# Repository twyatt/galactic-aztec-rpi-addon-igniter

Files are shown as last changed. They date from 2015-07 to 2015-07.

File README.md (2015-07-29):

# About
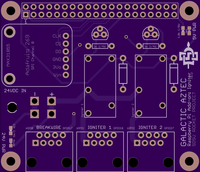
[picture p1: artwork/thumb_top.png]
OSHPark PCB Top Thumbnail

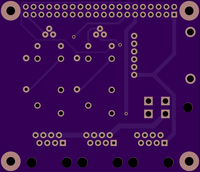
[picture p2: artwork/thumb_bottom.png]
OSHPark PCB Bottom Thumbnail


Custom Raspberry Pi Add-on board used for launching the [Galactic Aztec] rocket to interface with the [Galactic Aztec Igniter Connector]. The board was designed to be stackable with other add-on boards via the designated [pin configuration].

Custom EagleCAD parts on this board can be found in the [SDSU Rocket Eagle Libraries].

## Wiring
The igniter and break wires that ran from the add-on board to the rocket's igniter were [CAT6 cables] that ran thru [RJ45 couplers] and followed the following [T-568B] wiring configurations:

### Igniter
| Pin | Color | Function |
|:---:|:---:|:---:|
| 1 | Orange/White | Supply Voltage |
| 2 | Orange | Ground |
| 3 | Green/White  | Supply Voltage |
| 4 | Blue | Ground |
| 5 | Blue/White | Supply Voltage |
| 6 | Green | Ground |
| 7 | Brown/White  | Supply Voltage |
| 8 | Brown | Ground |

### Break Wire
| Pin | Color | Function |
|:---:|:---:|:---:|
| 1 | Orange/White | 3.3V |
| 2 | Orange | Signal |
| 3 | Green/White  | 3.3V |
| 4 | Blue | Signal |
| 5 | Blue/White | 3.3V |
| 6 | Green | Signal |
| 7 | Brown/White  | 3.3V |
| 8 | Brown | Signal |

# Bill of Materials
| Qty | Description | Part Number | Vendor |
|:---:|---|---:|---|
| 1 | Header Stacking 2x20 Tall 23mm | [1979] | Adafruit |
| 2 | Diode 50V 1A PTH | [1N4001FSCT-ND] | DigiKey  |
| 2 | Transistor NPN 40V 0.6A TO-92 PTH | [2N5551TAFSTB-ND] | DigiKey  |
| 3 | Jack RJ45 CAT5/CAT5e | [380-1046-ND] | DigiKey  |
| 1 | LED Red Vf=1.8V If=2mA 0603 | [475-1195-2-ND] | DigiKey  |
| 1 | Molex Mini Fit Jr. 4-pos Right Angle | [WM1352-ND] | DigiKey  |
| 1 | LED Red Vf=2V If=20mA 0603 | [754-1359-1-ND] | DigiKey  |
| 1 | Resistor 1.8kΩ 1/4W 1% 0603 | [P1.8KBYCT-ND] | DigiKey  |
| 1 | Resistor 1.2kΩ 2W 1% 2512 | [A116034CT-ND] | DigiKey  |
| 2 | Resistor 1k 1/4W 1% PTH | [RNF14FTD1K00CT-ND] | DigiKey  |
| 1 | Header Female 1x6 0.1" Pitch | [S7039-ND] | DigiKey  |
| 2 | Relay 5V 5A SPST-NO (1 Form A) | [Z945-ND] | DigiKey  |

[Galactic Aztec]: http://rocket.sdsu.edu/rockets
[Galactic Aztec Igniter Connector]: https://github.com/twyatt/galactic-aztec-igniter-connector
[pin configuration]: https://docs.google.com/spreadsheets/d/1zGslKhH-ZteeA8sbbTjQlF-Neb-wJ3quIlFH6I8Cvgs/edit?usp=sharing
[CAT6 cables]: http://amzn.com/B00DUYDFVY
[RJ45 connector pin configuration]: https://docs.google.com/spreadsheets/d/1SQShVjZaio6u5dARqMazgQztgd2wGieyxO2AVLGVz4Q/edit?usp=sharing
[RJ45 couplers]: http://amzn.com/B00GE1DHRC
[SDSU Rocket Eagle Libraries]: https://github.com/twyatt/SDSURocket-Eagle-Libraries
[T-568B]: https://en.wikipedia.org/wiki/TIA/EIA-568#Wiring
[1979]: http://www.adafruit.com/products/1979
[1N4001FSCT-ND]: http://www.digikey.com/product-detail/en/1N4001/1N4001FSCT-ND/1532742
[2N5551TAFSTB-ND]: http://www.digikey.com/product-detail/en/2N5551TA/2N5551TAFSTB-ND/973959
[380-1046-ND]: http://www.digikey.com/product-detail/en/SS-7188-NF/380-1046-ND/388308
[475-1195-2-ND]: http://www.digikey.com/product-detail/en/LS%20L29K-H1J2-1-Z/475-1195-1-ND/810356
[WM1352-ND]: http://www.digikey.com/product-search/en?x=0&y=0&lang=en&site=us&keywords=538-39-30-1040
[754-1359-1-ND]: http://www.digikey.com/product-detail/en/APG1608SURKC%2FT/754-1359-1-ND/1919171
[P1.8KBYCT-ND]: http://www.digikey.com/product-detail/en/ERJ-PA3F1801V/P1.8KBYCT-ND/5036145
[A116034CT-ND]: http://www.digikey.com/product-detail/en/5-2176070-1/A116034CT-ND/4280086
[RNF14FTD1K00CT-ND]: http://www.digikey.com/product-detail/en/RNF14FTD1K00/RNF14FTD1K00CT-ND/1975018
[S7039-ND]: http://www.digikey.com/product-detail/en/PPPC061LFBN-RC/S7039-ND/810178
[Z945-ND]: http://www.digikey.com/product-detail/en/G6B-1114P-US-DC5/Z945-ND/148724

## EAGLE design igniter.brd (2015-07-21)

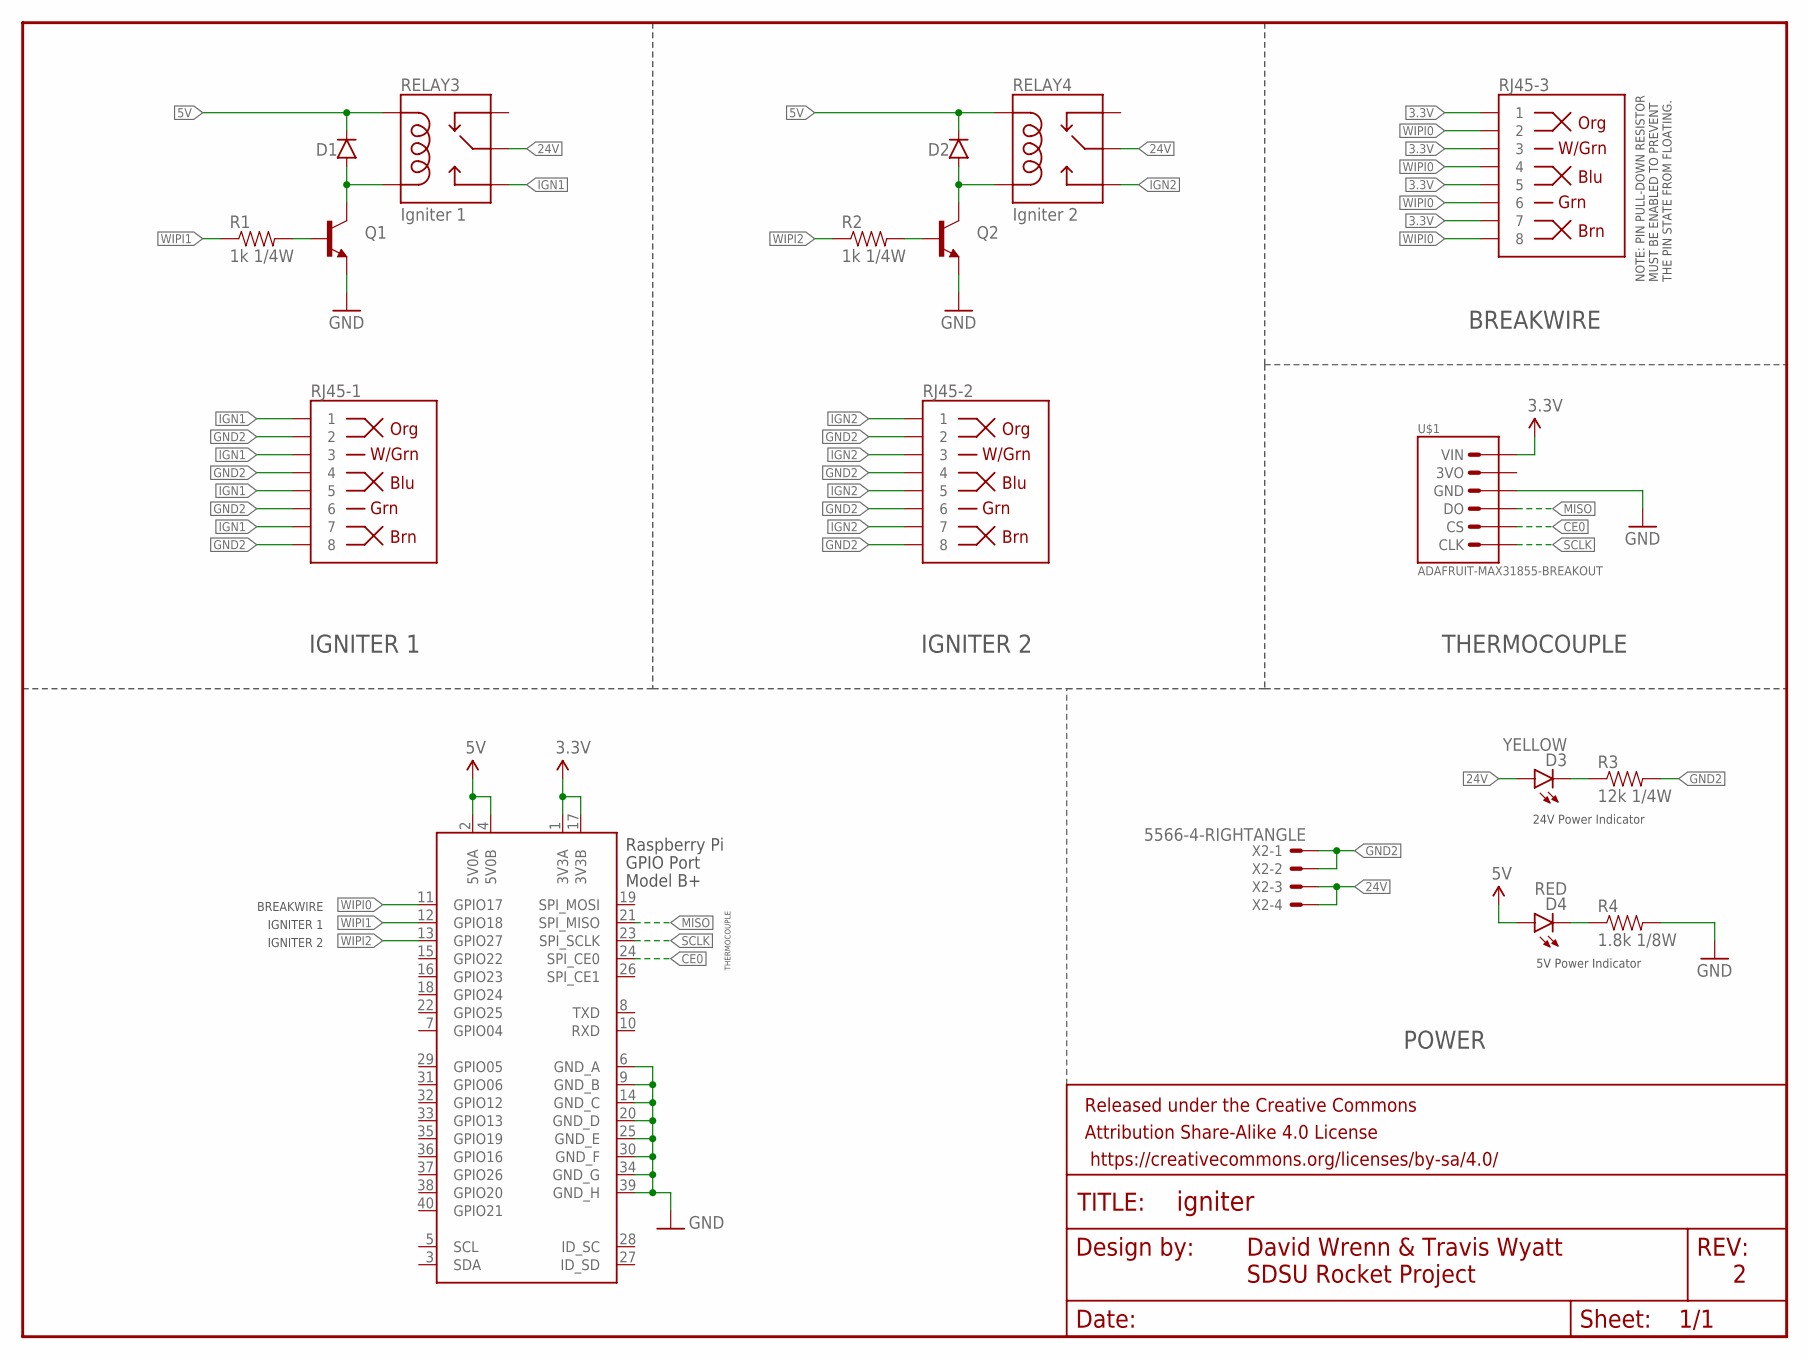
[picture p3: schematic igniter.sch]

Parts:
D1, D2: DIODEPTH; DIODE-1N4001
D3: YELLOW; LED-0603
D4: RED; LED-0603
FRAME1: FRAME-LETTER; CREATIVE_COMMONS
Q1, Q2: TRANSISTOR_NPNP2N2222A; TO-92
R1, R2: 1k 1/4W; AXIAL-0.3
R3: 12k 1/4W; 0603-RES
R4: 1.8k 1/8W; 0603-RES
RELAY3: Igniter 1; RELAY-G5Q
RELAY4: Igniter 2; RELAY-G5Q
RJ45-1, RJ45-2, RJ45-3: RJ45-8PTH; RJ45-8
U$1: ADAFRUIT-MAX31855-BREAKOUT; ADAFRUIT-MAX31855
X1: RASPI_BOARD_B+#_H; RASPI_BOARD_B+HAT
X2: 5566-4-RIGHTANGLE; 5566-4

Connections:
3.3V: RJ45-3.1, RJ45-3.3, RJ45-3.5, RJ45-3.7, U$1.VIN, X1.1 (3V3A), X1.17 (3V3B)
5V: D1.C, D2.C, D4.A, RELAY3.5 (COIL1), RELAY4.5 (COIL1), X1.2 (5V0A), X1.4 (5V0B)
24V: D3.A, RELAY3.2 (MAIN), RELAY4.2 (MAIN), X2.3, X2.4
CE0: U$1.CS, X1.24 (SPI_CE0)
GND: Q1.3 (E), Q2.3 (E), R4.2, U$1.GND, X1.6 (GND_A), X1.9 (GND_B), X1.14 (GND_C), X1.20 (GND_D), X1.25 (GND_E), X1.30 (GND_F), X1.34 (GND_G), X1.39 (GND_H)
GND2: R3.2, RJ45-1.2, RJ45-1.4, RJ45-1.6, RJ45-1.8, RJ45-2.2, RJ45-2.4, RJ45-2.6, RJ45-2.8, X2.1, X2.2
IGN1: RELAY3.3 (NO), RJ45-1.1, RJ45-1.3, RJ45-1.5, RJ45-1.7
IGN2: RELAY4.3 (NO), RJ45-2.1, RJ45-2.3, RJ45-2.5, RJ45-2.7
MISO: U$1.DO, X1.21 (SPI_MISO)
unnamed: Q1.2 (B), R1.P$2 (2)
unnamed: D1.A, Q1.1 (C), RELAY3.1 (COIL2)
unnamed: D3.C, R3.1
unnamed: D4.C, R4.1
unnamed: Q2.2 (B), R2.P$2 (2)
unnamed: D2.A, Q2.1 (C), RELAY4.1 (COIL2)
SCLK: U$1.CLK, X1.23 (SPI_SCLK)
WIPI0: RJ45-3.2, RJ45-3.4, RJ45-3.6, RJ45-3.8, X1.11 (GPIO17)
WIPI1: R1.P$1 (1), X1.12 (GPIO18)
WIPI2: R2.P$1 (1), X1.13 (GPIO27)

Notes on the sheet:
IGNITER 1
IGNITER 2
BREAKWIRE
POWER
THERMOCOUPLE
NOTE: PIN PULL-DOWN RESISTOR MUST BE ENABLED TO PREVENT THE PIN STATE FROM FLOATING.
David Wrenn & Travis Wyatt
SDSU Rocket Project
24V Power Indicator
5V Power Indicator

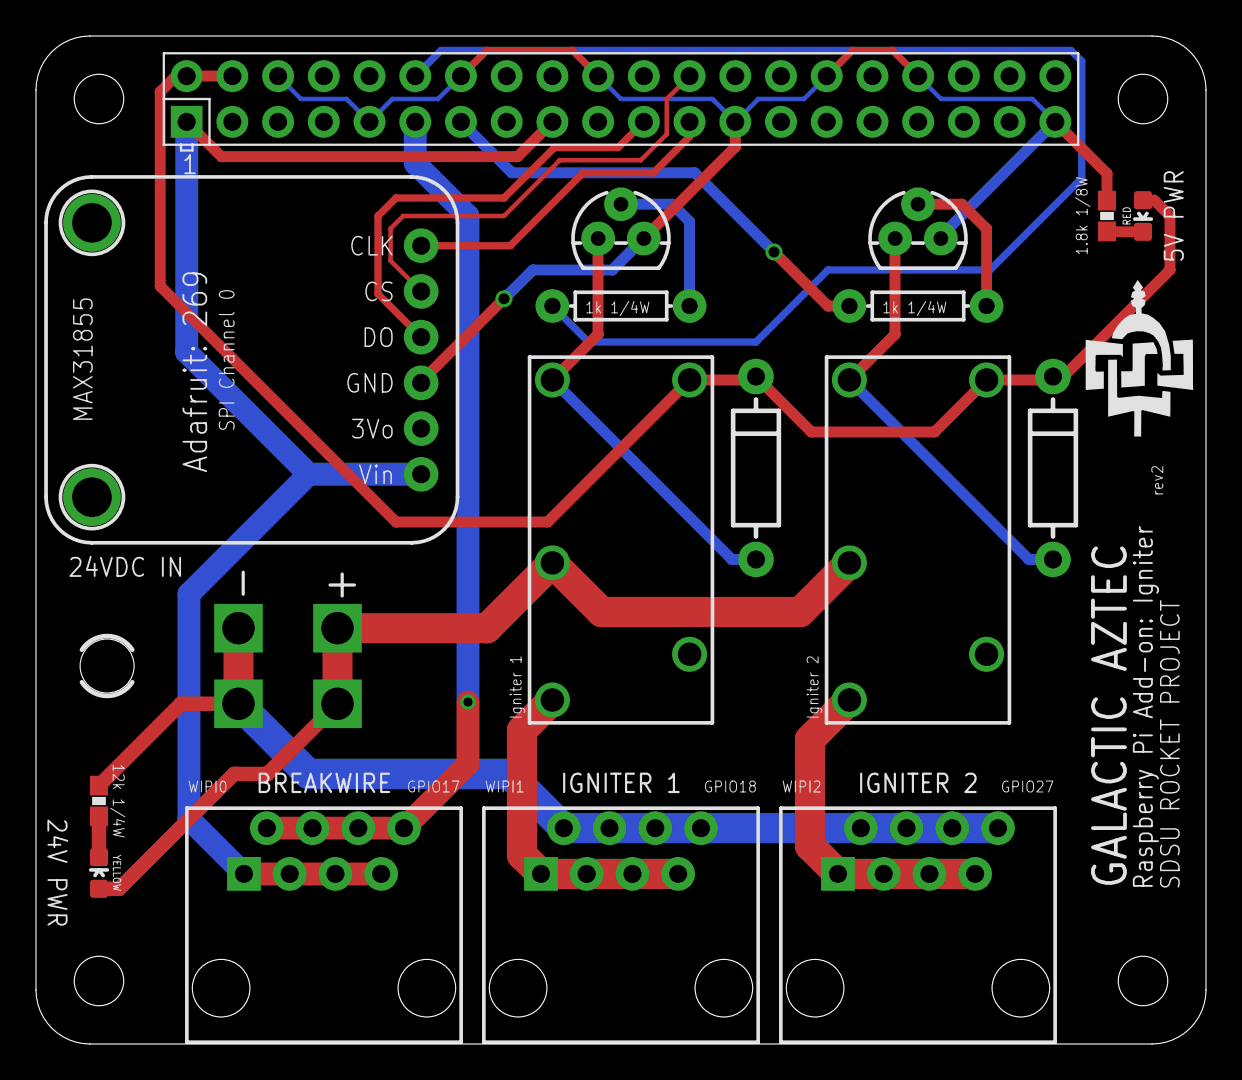
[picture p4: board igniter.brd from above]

Board: 2 copper layers, 65.0 x 56.0 mm, 19 parts (0 on the bottom side), 19 nets.

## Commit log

2015-07-18 Initial commit.
    [igniter.brd, igniter.sch]
2015-07-21 Power connector and resistor updates. Added PCB images (generated by OSHPark). Added README.md.
    [igniter.brd, igniter.sch]

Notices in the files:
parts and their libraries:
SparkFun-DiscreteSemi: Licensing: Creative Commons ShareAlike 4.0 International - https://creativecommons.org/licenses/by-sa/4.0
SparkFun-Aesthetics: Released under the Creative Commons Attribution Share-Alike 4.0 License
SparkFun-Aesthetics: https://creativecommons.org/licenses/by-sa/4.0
